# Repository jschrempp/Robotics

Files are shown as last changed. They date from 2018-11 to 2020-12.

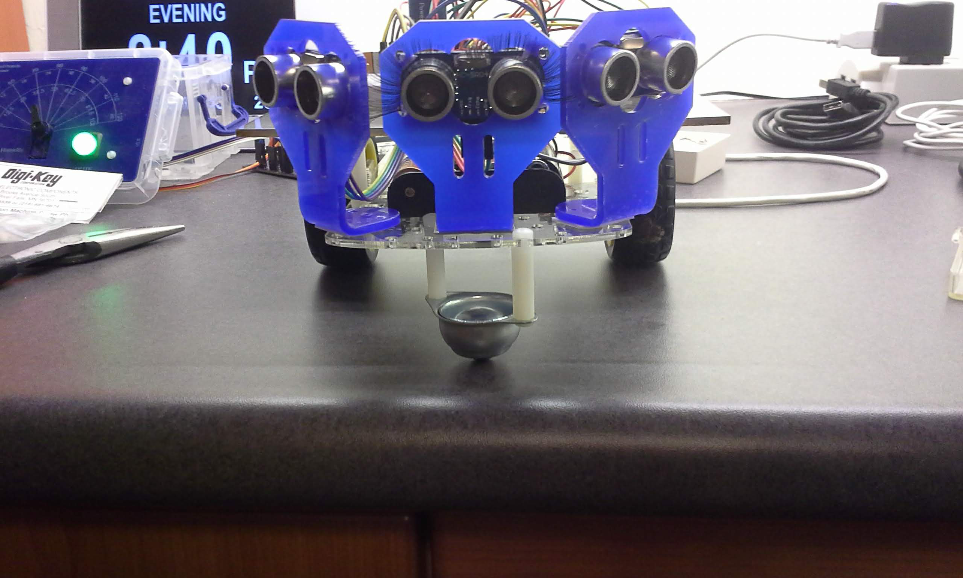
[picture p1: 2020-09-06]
Hardware/Caster_mounted_with_standoffs.jpg

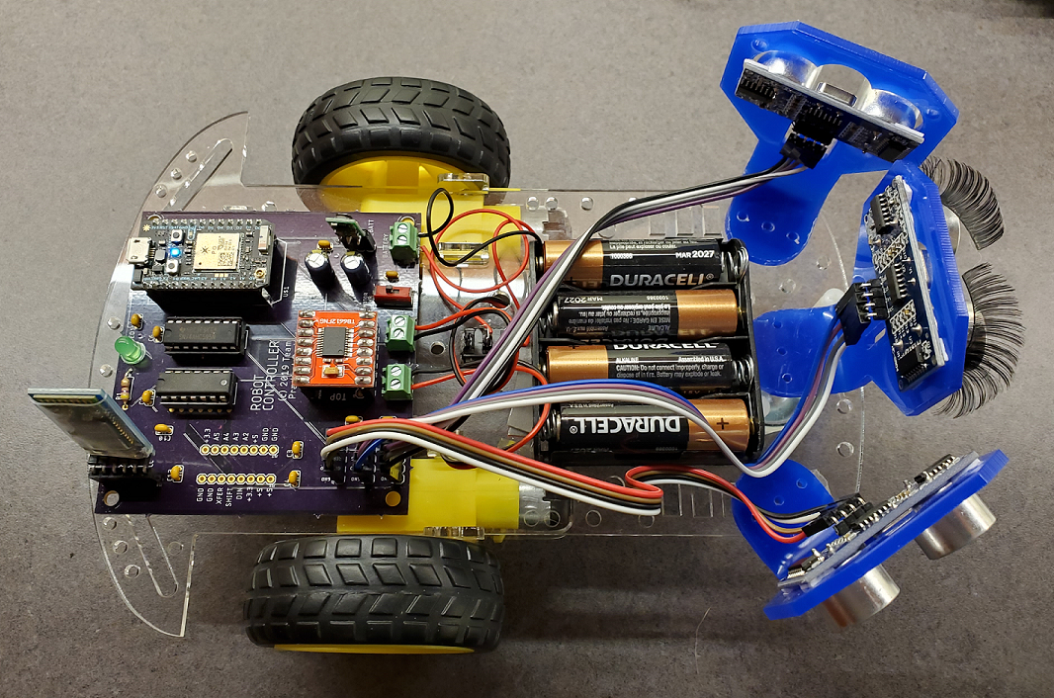
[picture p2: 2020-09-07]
Robot.png

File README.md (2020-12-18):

# Robotics
Hardware, firmware, software and documentation for low cost robotics experimentation and development using 
Particle Photon and MIT App Inventor 2.

## Story
We (Team Practical Projects) wanted to explore the capabilities and limitations of very inexpensive robot 
technology.  We obtained a basic robot kit for about $12.  This kit contains a plastic chassis, two drive
motors and drive wheels, a front caster wheel, a 4 AA cell battery holder, an on/off switch, and mounting
and assembly hardware.  

In order to run, test and explore the robot, we designed and built a Particle Photon-based printed circuit
board.  We chose the Particle Photon for our microcontroller because of Arduino
code compatibility, the ability to flash new firmware over WiFi, and Particle's IoT cloud functionality.
However, we used an inexpensive bluetooth module for basic communication with the robot (vs. the Particle Cloud)
because we wanted to experiment with our robot both indoors and outdoors; the latter where there is no
WiFi available.

The printed circuit board that we designed for this project contains all of the electronics needed to control
and monitor the robot.  This board includes:
1. The Particle Photon.
2. A buck power converter (so that the electronics can be powered from the robot's batteries).
3. Interface circuitry for three HC-SR04 ultrasonic distance sensors.
4. An HC-05 bluetooth module.
5. A dual H-bridge motor controller capable of driving the two motors on the robot.
6. Expansion capability for future development.

We wrote an Android app (in MIT App Inventor 2) to communicate with the robot and control its motion
manually and in an automatic, self-navigating, obstacle-avoiding mode.  

This repository contains complete, open source documention for building and operating this robot.

## Findings
1. The cheap caster wheel that came with the robot kit had a tendency to bind up and send the robot off
at odd angles.  Our solution was to find a suitable ball caster that replaces the robot kit front wheel.

2. In order for the robot to self-navigate, it needs to take distance measurements to obstacles both in
front of the robot and on both sides of the robot.  We tried using a single ultrasonic sensor mounted on a servo but
we found that the overall measurment cycle was too slow for our purposes.  We opted for using three, fixed
mounted ultrasonic distance sensors: one in front and two facing to each side of the robot.  These sensors
are cheap enough for us to use them this way. The side sensors are needed in the event that the robot approaches 
a side wall at a heavily oblique angle.  In particular, we have found that these sensors should face the 
side somewhere between 60 degrees and 90 degrees from the robot's front. We were unable to determine a single 
optimal angle for the side avoidance sensors.  We believe that there is too much dependancy on wall reflectivity 
and corner angles to establish a single, best sensor configuration (owning, we believe, to multi-path effects -- see below).

3. We found that there are dead spots between the three ultrasonic sensors. If the robot approaches an obstacle in 
the dead spot (e.g. a table leg), it will get hung up. We also found that the ultrasonic sensors are subject to multi-path effects.  The
ultrasonic signals can bounce off of multiple walls before returning to the sensor, resulting in incorrect distance measurements.
We also found that it is possible for a multi-path signal reflection from one sensor to be detected by another
sensor.  We created a delay of 1 millisecond between sensor readings in order to reduce this effect.  

4. We found that different surfaces reflect different amounts of ultrasonic energy.  Some surfaces (generally
soft surfaces) are poor reflectors of ultrasonic signals while other surfaces (generally hard surfaces) perform much better.
Unsurprisingly, the robot works best when tested against hard vertical walls set at right angles to each other.

5. Given the limitations of ultrasonic distance sensors, we investigated alternatives but we were unable to find
any suitable alternative sensors in the low cost range.  We tried infrared distance sensors that work by measuring
the strength of reflected infrared energy, but we found that the performance was highly sensitive to the color
of a surface.  White walls worked well, whereas black walls did not work at all (absorbed almost all of the
infrared energy).  We concluded that the best sensor technology would likely be lidar, but the cost of lidar
technology far exceeds the cost constriants of this project.

6. We found that weight distribution on the robot body impacts robot traction. The heaviest item on the 
robot platform are the batteries.  It would be best to place the battery holder directly over axis between
the two rear drive wheels. However, the parts don't fit well in this configuration.  The parts fit best
in the conguration shown on the photo "Robot.png" in this repository; however, traction is not
optimal with this configuration of parts.  Traction is improved by placing the printed circuit board
up front and the battery holder in the back.

7. The overall ability of the robot to self-navigate and avoid obstacles is fairly impressive, given the
limitations of the sensing capability.  The robot has the ability to find a way out from most obstacles,
including corners, chair and table legs, etc. Self navigation is not perfect, however.
The robot pivots on an axis between the rear drive wheels and not the center of the chassis, which results
in the pivot arc being longer than we had expected.  A 4 wheel
robot or a robot based on a tank chassis might obviate this problem.  Alternatively, adding a rear sensor and
firmware to back the robot out of a jam (in lieu of pivoting the robot to move out of a jam forward) might
improve this behavior.

8. The strength of the motors and the size of the drive and caster wheels limit the types of surfaces where the robot
can operate successfully.  A flat hard surface or a very low pile office carpet work well.  Plush carpet and 
height transitions do not work well with this robot. A tank chassis might allow the robot to operate over
small height transitions and on plush surfaces.

We have documented the robot's behavior in autonomous navigation mode (AUTO) in a series of six videos that 
you can view, beginning here:

https://www.youtube.com/watch?v=S9v4ddf_cKs&list=PLz4TQp3CqyALdgTUBRFCJkOn_9tXRT2St

In addition to autonomous mode, the Robot can be manually steered via the app supplied with this project.

## Conclusions
Our conclusion is that the robot can successfully navigate autonomously over a fairly wide range of challenging
conditions, given the limitations of the low cost hardware used.

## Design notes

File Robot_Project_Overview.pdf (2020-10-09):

# Robot Project Overview

By: Jim Schrempp and Bob Glicksman; v2, 10/8/2020

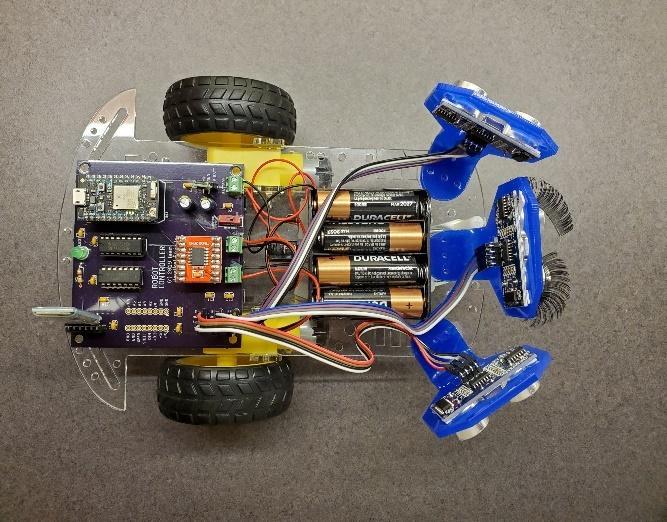
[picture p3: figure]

© 2020 Team Practical Projects, Bob Glicksman and Jim Schrempp. All rights reserved.

NOTICE: Use of this document is subject to the terms of use described in the document
“Terms_of_Use_License_and_Disclaimer ” that is included in this release package. This document can be found at:

https://github.com/TeamPracticalProjects/Robotics/blob/master/Terms_of_Use_License_and_Disclaimer.pdf

© 2020, Team Practical Projects, Jim Schrempp AND Bob Glicksman; all rights reserved. Subject to “Terms of Use, License and Disclosure”

TABLE OF CONTENTS.

TABLE OF CONTENTS. | 1
1. | DOCUMENT OVERVIEW. | 2
2. | REPOSITORY OVERVIEW. | 2
| Repository Structure. | 2
| Suggested Use of the Documents. | 4
3. | ROBOT PROJECT ARCHITECTURE AND COMPONENTS. | 5

1.DOCUMENT OVERVIEW.

This document provides an overview of the Robot project. The Team Practical Projects Robot is designed for learning and entertainment. You can control the Robot manually, via an Android App, or have it navigate autonomously, sensing and avoiding obstacles as it goes. The Robot is based upon the Particle¹ Photon; an inexpensive, but advanced, 32 bit microcontroller with built-in WiFi capability. The Photon’s WiFi capability is used in this project to allow new firmware to be flashed to the Robot “over-the-air”, without the need for wired connections. The Robot itself has been designed for Bluetooth control, so that it can operate anywhere, regardless of whether a WiFi connection is present or not.

Section 2 of this document provides a guide to this Repository. The Robot is an open source project and we provide complete documentation, including source code for the Robot firmware and controlling App software, and CAD files for the printed circuit board (PCB) that holds the Robot’s electronics. We also provide a complete build and installation instruction manual and a user manual.

Section 3 of the document provides an overview of the system architecture. The “system” is very simple, consisting of the Robot hardware, the Robot’s internal firmware for the Photon microcontroller, and an Android App that is used to control and monitor the Robot.

2.REPOSITORY OVERVIEW.

This section describes the contents of this repository. This is an open source project. The files in this repository contain source code, hardware schematics and CAD files, and documentation.

Repository Structure.

GitHub.com/TeamPracticalProjects/Robotics
| -- “README.md”: the overview read-me file that is displayed on the GitHub project page. The file format is markdown (.md)
| -- “Terms_of_Use_License_and_Disclaimer”: the terms of use that you must agree
to in order to use the contents of this repository. The file format is portable document format (.pdf)
| -- “Robot_Project_Overview.pdf”: This document. The file format is portable document format (.pdf)
| -- “Robot.png”: a photo of the Robot. The file format is .png
| -- Software (folder containing all software and firmware):
| -- AI2_App (folder containing the app software)
| -- compiled (folder)
| -- “BasicRobotControl.apk”: Android install package

1 https://www.particle.io/

for the app. Load this file onto your Android smartphone and tap on it to install the app. The file format is android application package (.apk)
| -- src (folder)
| -- “BasicRobotControl.aia”: Source code for the app.
The source code is in the MIT App Inventor 2 graphical language. Import this file into your MIT App Inventor 2 IDE in order to view and/or edit the app source code. The file format is AI2 source code format (.aia).
| -- Firmware (folder containing the firmware for the Photon)
| -- “.gitignore”. This file is used to ignore some files that should not be added to your repository. It is in plain text format.
| -- “AutonomousRobotParticle.code-workspace”. This file is automatically added by the Particle Workbench IDE and you do not need to do anything with it. If you use the Particle Workbench you can open this file to restore a development environment. It is in plain text format.
| -- “project.properties”. This file is automatically added by the Particle Workbench IDE and you do not need to do anything with it. It is in plain text format.
| -- src (folder)
| -- “AutonomousRobotParticle.ino”: Particle Photon source code for the firmware that is loaded onto the Photon. The file format is Arduino source code format (.ino), which is pure text. Copy the contents of this file into the Particle Web IDE or the Particle Workbench in order to compile the firmware and flash it onto your Photon.
| -- Documents (folder containing project documentation)
| -- “Robot_Build_And_Installation_Instructions.pdf”: Document
that details how to build, install and test the project. The file format
is portable document format (.pdf).
| -- “MFG_robot_assembly_instructions.pdf”: The robot chassis manufacturer’s instruction sheet for how to assemble the robot chassis kit. The file format is portable document format (.pdf).
| -- “Robot_User_Manual”: User manual for the Robot and its associated
App. The file format is portable document format (.pdf).
| -- Hardware (folder containing project hardware files)
| -- “Robot_Parts_List.pdf”: A parts list for the Robot with links to sources for the parts. The file format is portable document format (.pdf).
| -- “Photon_Robot_View_1.jpg”: A high resolution, top view photo of the Completed Robot. The file format is JPEG (.jpg).
| -- “Photon_Robot_View_2.jpg”: A high resolution, side view photo of the Completed Robot. The file format is JPEG (.jpg).

| -- “Caster_mounted_with_standoffs.jpg”: A photo showing how the ball caster is attached to the Robot chassis. The file format is JPEG (.jpg). | -- Photon PCB (folder)
| -- Eagle_Files (folder)
| -- “RobotController.sch”: Cadsoft Eagle schematic. File format is Eagle schematic (.sch).
| -- “RobotController.brd”: Cadsoft Eagle board layout. File format is Eagle board (.brd).
| -- “Robot_Controller_PCB_Parts_List.pdf”: A parts list for the Robot PCB. The assembled PCB is itself a part on the
Robot_Parts_List in the Documents folder. The file
format is portable document format (.pdf).
| -- “Robot_Controller_Schematic.pdf”: This is a PDF version of The Robot PCB schematic, for those who don’t have Eagle. The file format is portable document format (.pdf).

Suggested Use of the Documents.

We suggest that you read the documents (.pdf files) contained in this repository in the following order:

- Terms_of_Use_License_and_Disclaimer: read and agree to everything in this document before proceeding further this this project.
- Robot_Project_Overview: read through this document to familiarize yourself with what this project is about and ensure that you can successfully complete, install and use this project before you invest further in it.
- Robot_Build_And_Installation_Instructions: follow the steps in this document to build the electronics, build the Robot chassis and install its components, install the Photon firmware, install the App software, and perform a basic test that things are working.
- Robot_User_Manual: consult this manual to learn how about the switches on the Robot and learn to use the App.

# 3.ROBOT PROJECT ARCHITECTURE AND

COMPONENTS.

The overall architecture of the Robot system is shown is figure 3-1. The major components of the system are:

- The Robot itself.
- An Android² device (phone or tablet) running the Robot control app.
- A development computer (desktop, laptop, tablet) for compiling the Robot firmware source code and flashing the resulting firmware onto the Robot’s Photon module over the Internet.

This repository contains Particle source code for the Robot. Particle’s source code is written in Particle’s firmware language which is Arduino compatible and compiled with a C++ compiler. This source code can be compiled for the Photon using either Particle’s Web IDE or Particle’s Workbench IDE. After compilation, either of these IDE’s can be used to flash the resulting executable firmware onto the Photon using Particle’s over-the-air (OTA) flashing capability via the Particle Cloud. Instructions for doing this are contained in the document “Robot_Build_And_Installation_Instructions.pdf” which can be found in the “Documents” folder in this repository. Note that the Photon uses WiFi to communicate with the Particle cloud over the Internet, so flashing of new firmware onto the Robot can only take place where the Photon has access to WiFi and where the Photon is actually on the WiFi network. Particle makes this process extremely easy and their documentation is excellent (see: https://docs.particle.io/photon/).

After firmware is flashed to the Photon, the Robot no longer has to be in WiFi range in order to operate. The Robot is battery powered and communicates with the App using Bluetooth. The firmware places the Robot’s Photon in “Semi-Automatic mode” which means that the firmware does not need to be connected to the Particle Cloud in order to operate. However, when you want to flash new firmware the Photon will need to be connected to WiFi; do this by placing the Photon into “safe mode”. Instructions for doing this are contained in the document “Robot_Build_And_Installation_Instructions.pdf” which can be found in the “Documents” folder in this repository.

2 Sorry; an iOS version of the Robot app is not available at this time.

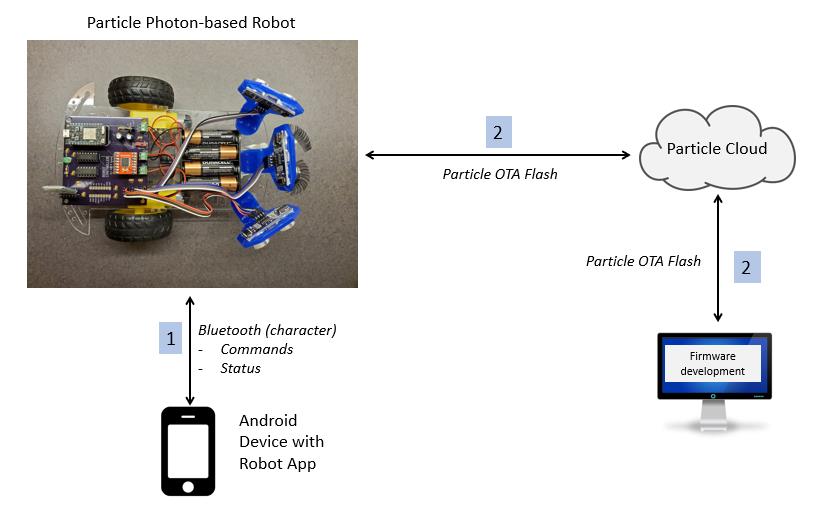
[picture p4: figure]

Figure 3-1. Robot System Components.

Figure 3-2 is a closeup photo of the Robot. The Robot consists of three major components:

- The Robot Chassis. This is a low cost kit that you purchase over the Internet. It contains the Robot body and mounting hardware, two motors with encoders and wheels, a front caster wheel (which is not used; we replace this with a ball caster for better performance), a 4 – AA battery holder, and a power on/off switch.
- The Robot PCB. This printed circuit board (PCB) needs to be assembled based upon the parts list in the Hardware/Photon PCB folder in this repository.
- Ultrasonic Distance Sensors: The Robot uses three HC-SR04 ultrasonic distance sensors for autonomous navigation. The sensors and their mounts are included in the “Robot_Parts_List.pdf” document in the Hardware folder in this repository.

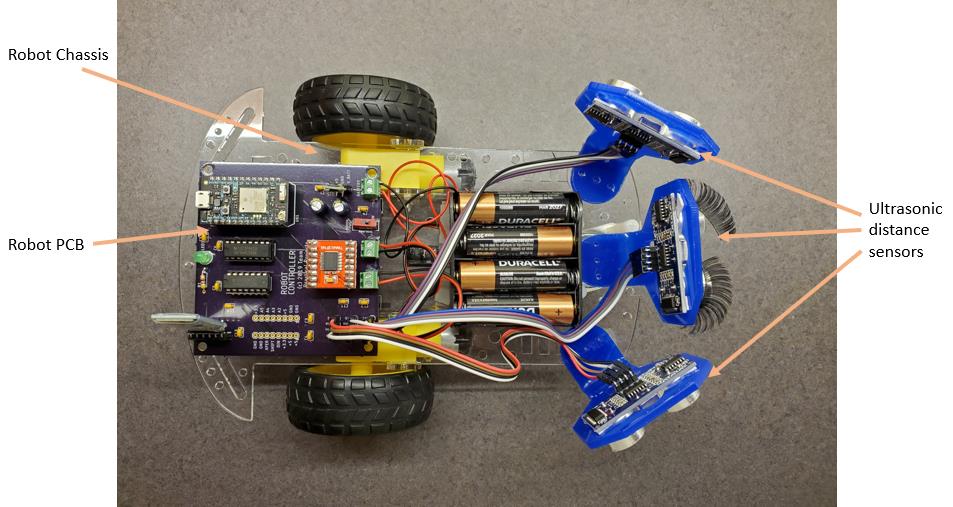
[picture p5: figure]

Figure 3-2. Robot closeup.

The final component of this Robot System is an app that runs on an Android device (phone or tablet). A screen shot of the App (in AUTO mode) is given in figure 3-3. Instructions for using the App are contained in the document “Robot_User_Maual.pdf” which is in the Documents folder in this repository.

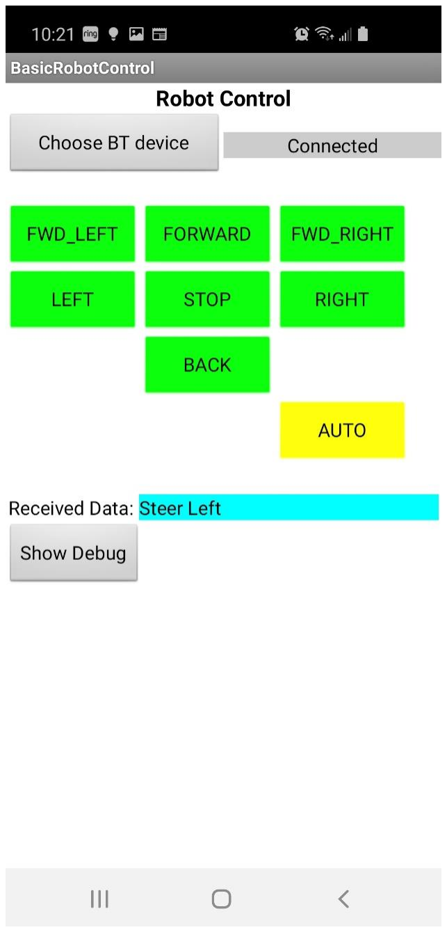
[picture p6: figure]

Figure 3-3. App screen shot (AUTO mode).

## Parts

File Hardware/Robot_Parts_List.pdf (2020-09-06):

ITEM | QTY | DESCRIPTION | VENDOR | LINK | UNIT COSTEXTENDED COST | ALTERNATE | NOTES
1 | 1 Robot Kit | ebay | https://www.ebay.com/itm/New-Smart-Motor-Robot-Car-Battery-Box-
Chassis-Kit-Speed-Encoder-For-
| | | | Arduino/233251245264?_trkparms=aid%3D555018%26algo%3DPL.SIM%26 ao%3D2%26asc%3D225074%26meid%3D354efebec4a74c81bac7d57ae2ba 87a6%26pid%3D100677%26rk%3D2%26rkt%3D30%26mehot%3Dnone%26s d%3D223697370099%26itm%3D233251245264%26pmt%3D1%26noa%3D0 %26pg%3D2386202%26algv%3DSimplAMLv5PairwiseWeb&_trksid=p23862

02.c100677.m4598 (https://www.ebay.com/itm/New-Smart-Motor-Robot-Car-Battery-Box-Chassis-Kit-Speed-Encoder-For-Arduino/233251245264)

$11.99 | $11.99

2

1

Robot Electronics PCB | Team Practical
Projects
| https://github.com/TeamPracticalprojects/Robotics/tree/master/Hardware | $104.02 | $104.02 | Build from our instructions and parts list. Most of the cost is in the bare PCB. These can be obtained for much lower price, e.g. from JCLPCB.com
3 | 1 HC_SR04 Ultrasonic Distance
Sensor
Amazon (Aokin) | https://www.amazon.com/dp/B07V6X647X/ref=dp_prsubs_3 | $7.99 | $7.99 | Get 5 pcs - need 3 pcs for robot
4 | 1 HC_SR04 Mount | Amazon (SenMod) https://www.amazon.com/gp/product/B01FDGU0GY/ref=ppx_yo_dt_b_asi
| n_title_o01_s00?ie=UTF8&psc=1 (https://www.amazon.com/gp/product/B01FDGU0GY/ref=ppx_yo_dt_b_asin_title_o01_s00?ie=UTF8&psc=1) | $7.99 | $7.99 | Get 5 pcs - need 3 pcs for robot
5 | 1 Ball Caster | Amazon
(Quickbuying)

https://www.amazon.com/gp/product/B07H5HC232/ref=ppx_yo_dt_b_asi
n_title_o00_s00?ie=UTF8&psc=1 (https://www.amazon.com/gp/product/B07H5HC232/ref=ppx_yo_dt_b_asin_title_o00_s00?ie=UTF8&psc=1)
$13.96 | $13.96 | Get 5 pcs - need 1 pcs for robot
6 | 1 #6 standoff, 1", F-F threaded Amazon | https://www.amazon.com/Lyn-Tron-Stainless-Steel-Female- Length/dp/B00PKI5NBI/ref=sr_1_4?crid=UX9AUCCKNWVI&dchild=1&keyw ords=Standoffs&pd_rd_r=a725047d-5a9c-4a79-93de- afee4ef9def9&pd_rd_w=ahVbR&pd_rd_wg=F3jHJ&pf_rd_p=91473338- a775-4a82-9600- 6767cae1f29a&pf_rd_r=ERK8K42QKTSWNMWN82M6&pid=tlRIAA7&qid=1 599417165&refinements=p_n_feature_twenty-eight_browse- bin%3A19043670011%2Cp_n_feature_fourteen_browse- bin%3A11433959011%2Cp_n_material_browse%3A17548970011&s=indust rial&sprefix=standoffs%2Cindustrial%2C274&sr=1-4
$21.58 | $21.58 | Get 10 pcs - need 2 pcs for robot
7 | 1 #6-32 screw, 1/4" | https://www.amazon.com/Stainless-Machine-Finish-Phillips- Threads/dp/B000FN3PKY/ref=sr_1_5?dchild=1&keywords=Screws&pd_rd_ r=6748bd84-aae1-44ee-80ad- aafba47a2747&pd_rd_w=9Gcuj&pd_rd_wg=neCmw&pf_rd_p=91473338- a775-4a82-9600- 6767cae1f29a&pf_rd_r=VT29VAKN079G8PEDE4XA&pid=H63dCos&qid=159 9417001&refinements=p_n_feature_twenty-eight_browse- bin%3A19043642011%2Cp_n_feature_fourteen_browse- bin%3A11433959011&s=industrial&sr=1-5 (https://www.amazon.com/Stainless-Machine-Finish-Phillips-Threads/dp/B000FN3PKY?pid=H63dCos&s=industrial)
$8.83 | $8.83 | Get 100 pcs - need 4 pcs for robot
8 | 1 strip of 40 female-female 6"
Adafruit | https://www.adafruit.com/products/266 | $3.95 | $3.95
9 | 4 AAA battery | Amazon | https://www.amazon.com/Duracell-CopperTop-Batteries-all-purpose-
household/dp/B00A4BBCIE/ref=sr_1_20?crid=2TTNFSC11DEIH&dchild=1&k eywords=aaa+battery&qid=1599416125&s=electronics&sprefix=AAA+batte ry%2Celectronics%2C236&sr=1-20 (https://www.amazon.com/Duracell-CopperTop-Batteries-all-purpose-household/dp/B00A4BBCIE?s=electronics)
$4.34 | $17.36
10 misc | #26 wire (red and black) | Misc
11 misc | double sided tape | Misc

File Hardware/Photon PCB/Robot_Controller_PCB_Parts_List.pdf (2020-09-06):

ITEM | QTY | DESCRIPTION | VENDOR | LINK | UNIT COSTEXTENDED COST | ALTERNATE | NOTES
1 | 1 Robot Controller PCB | OSHPark | https://oshpark.com/orders/nxFe79wD | $53.35 | $53.35 | Must purchase 3 boards for $53.35
2 | 1 Particle Photon with headers Particle | https://www.amazon.com/Particle-
| | | | Reprogrammable-Development-
Prototyping-
| | | | Electronics/dp/B016YNU1A0?ref_=b l_dp_s_web_14204923011 (https://www.amazon.com/Particle-Reprogrammable-Development-Prototyping-Electronics/dp/B016YNU1A0)
$19.00 | $19.00
3 | 2 Female header, 12 position | Pololu | https://www.pololu.com/product/1
| | | 030 (https://www.pololu.com/product/1030)
$0.79 | $1.58 https://www.digikey.com/product-
detail/en/sullins-connectorsolutions/PPPC121LFBN-RC/S7045-ND/810184 (https://www.digikey.com/product-detail/en/sullins-connector-solutions/PPPC121LFBN-RC/S7045-ND/810184)
4 | 1 74HC595 shift register, 16 pin DIP | Sparkfun | https://www.sparkfun.com/product s/13699 (https://www.sparkfun.com/products/13699)
$0.95 | $0.95 https://www.digikey.com/products/en
/integrated-circuits-ics/logic-shiftregisters/712?k=74ahc595&k=&pkeyw ord=74ahc595&sv=0&pv7=6&s=435&p v16=6512&sf=1&quantity=&ColumnSo rt=0&page=1&pageSize=25 (https://www.digikey.com/products/en/integrated-circuits-ics/logic-shift-registers/712?k=74ahc595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)
5 | 1 IC DIP socket, 16 pin | Sparkfun | https://www.sparkfun.com/product s/7938 (https://www.sparkfun.com/products/7938)
$0.50 | $0.50 https://www.digikey.com/product-
detail/en/on-shore-technologyinc/ED16DT/ED3046-5-ND/4147596 (https://www.digikey.com/product-detail/en/on-shore-technology-inc/ED16DT/ED3046-5-ND/4147596)
6 | 1 74AHCT125 level converter, 14 pin DIP | Digikey | https://www.digikey.com/products/ en/integrated-circuits-ics/logic- buffers-drivers-receivers- transceivers/704?k=74ahct125&k=& pkeyword=74ahct125&sv=0&pv7=6 &s=465&pv16=6510&sf=1&quantity =&ColumnSort=0&page=1&pageSize =25 (https://www.digikey.com/products/en/integrated-circuits-ics/logic-buffers-drivers-receivers-transceivers/704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)
$0.40 | $0.40
7 | 1 IC DIP socket, 14 pin | Sparkfun | https://www.sparkfun.com/product s/7939 (https://www.sparkfun.com/products/7939)
$0.50 | $0.50 https://www.digikey.com/product-
detail/en/on-shore-technologyinc/ED14DT/ED3045-5-ND/4147595 (https://www.digikey.com/product-detail/en/on-shore-technology-inc/ED14DT/ED3045-5-ND/4147595)
8 | 1 TB6612FNG dual motor driver module | Pololu | https://www.pololu.com/product/7
| | | 13 (https://www.pololu.com/product/713)
$3.33 | $3.33 https://www.sparkfun.com/products/1
4450 (https://www.sparkfun.com/products/14450)
9 | 2 Female header, 8 position | Pololu | https://www.pololu.com/product/1
| | | 018 (https://www.pololu.com/product/1018)
$0.59 | $1.18 https://www.digikey.com/product-
detail/en/sullins-connectorsolutions/PPPC081LFBN-RC/S7041-ND/810180 (https://www.digikey.com/product-detail/en/sullins-connector-solutions/PPPC081LFBN-RC/S7041-ND/810180)
10 | 1 5 volt step-up/step-down voltage regulator; S9V11F5 | Pololu | https://www.pololu.com/product/2
| | | 836 (https://www.pololu.com/product/2836)
$5.95 | $5.95
11 | 1 Female header, 3 position | Pololu | https://www.pololu.com/product/1
| | | 013 (https://www.pololu.com/product/1013)
$0.34 | $0.34 https://www.digikey.com/product-
detail/en/sullins-connectorsolutions/PPPC031LFBN-RC/S7036-ND/810175 (https://www.digikey.com/product-detail/en/sullins-connector-solutions/PPPC031LFBN-RC/S7036-ND/810175)

Must purchase mimimum of 5 connectors from Pololu

12 | 1 Bluetooth Module, HC-05 | Amazon (HiLetGo) https://www.amazon.com/gp/produ ct/B071YJG8DR/ref=ppx_yo_dt_b_a sin_title_o02_s00?ie=UTF8&psc=1 (https://www.amazon.com/gp/product/B071YJG8DR/ref=ppx_yo_dt_b_asin_title_o02_s00?ie=UTF8&psc=1)
$8.95 | $8.95
13 | 1 Female header, 6 position | Pololu | https://www.pololu.com/product/1
| | | 016 (https://www.pololu.com/product/1016)
$0.49 | $0.49 https://www.digikey.com/product-
detail/en/sullins-connectorsolutions/PPPC061LFBN-RC/S7039-ND/810178 (https://www.digikey.com/product-detail/en/sullins-connector-solutions/PPPC061LFBN-RC/S7039-ND/810178)

Must purchase minimum of 2 connectors from Pololu

14 | 1 Male breakable header; 0.1"
pitch; 40 position
Sparkfun | https://www.sparkfun.com/product
s/116 (https://www.sparkfun.com/products/116)

$0.00 https://www.digikey.com/product-detail/en/wurth-electronicsinc/61304011121/732-5334-
ND/4846884 (https://www.digikey.com/product-detail/en/wurth-electronics-inc/61304011121/732-5334-ND/4846884)

For connecting ultrasonic distance sensor, HC-SR04; need 12 pins total

15 | 1 LED, 5 MM | Sparkfun | https://www.sparkfun.com/product s/9592 (https://www.sparkfun.com/products/9592)
$0.35 | $0.35 | Green LED is preferred but any color will do
16 | 1 Resistor, 470 ohm (footprint: 0207/10) | Digikey | https://www.digikey.com/product- detail/en/stackpole-electronics- inc/CF14JT470R/CF14JT470RCT- ND/1830342 (https://www.digikey.com/product-detail/en/stackpole-electronics-inc/CF14JT470R/CF14JT470RCT-ND/1830342)
$0.10 | $0.10
17 | 2 Capacitor, 100 uF; footprint
E2, 5-6E
Sparkfun | https://www.sparkfun.com/product
s/96 (https://www.sparkfun.com/products/96)
$0.35 | $0.70 https://www.digikey.com/products/en
?keywords=P10269-ND (https://www.digikey.com/products/en?keywords=P10269-ND)

Electrolytic, min 20 volt rating, 0.1" center-center lead pitch

18 | 11 Capacitor, 0.1 uF; footprint
C025-024X044
Sparkfun | https://www.sparkfun.com/product
s/8375 (https://www.sparkfun.com/products/8375)
$0.25 | $2.75 https://www.digikey.com/product-
detail/en/kemet/C315C104M5U5TA/3 99-4151-ND/817927 (https://www.digikey.com/product-detail/en/kemet/C315C104M5U5TA/399-4151-ND/817927)

Ceramic, min 10 volt rating, 0.1" center-center lead pitch

19 | 3 PCB screw terminal, 2
position, 3.5 mm pitch
Sparkfun | https://www.sparkfun.com/product
s/8084 (https://www.sparkfun.com/products/8084)
$0.95 | $2.85 https://www.pololu.com/product/244
4 (https://www.pololu.com/product/2444)

https://www.digikey.com/product-detail/en/wurth-electronicsinc/691214110002/732-2747-ND/2508516 (https://www.digikey.com/product-detail/en/wurth-electronics-inc/691214110002/732-2747-ND/2508516)
20 | 1 PCB mount switch, SPDT
(11.6x4.0 mm)
Sparkfun | https://www.sparkfun.com/product
s/9609 (https://www.sparkfun.com/products/9609)
$0.75 | $0.75 https://www.pololu.com/product/140
8 (https://www.pololu.com/product/1408)

https://www.digikey.com/product-detail/en/nkkswitches/SS12SDP4/360-2922-ND/1054800 (https://www.digikey.com/product-detail/en/nkk-switches/SS12SDP4/360-2922-ND/1054800)

TOTAL | $104.02

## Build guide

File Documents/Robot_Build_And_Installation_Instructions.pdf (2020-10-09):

# Robot Build and Installation Instructions

By: Jim Schrempp and Bob Glicksman; v3, 10/8/2020


© 2020 Team Practical Projects, Bob Glicksman and Jim Schrempp. All rights reserved.

NOTICE: Use of this document is subject to the terms of use described in the document
“Terms_of_Use_License_and_Disclaimer ” that is included in this release package. This document can be found at:

https://github.com/TeamPracticalProjects/Robotics/blob/master/Terms_of_Use_License_and_Disclaimer.pdf

© 2020, Team Practical Projects, Jim Schrempp AND Bob Glicksman; all rights reserved. Subject to “Terms of Use, License and Disclosure”

TABLE OF CONTENTS.

TABLE OF CONTENTS. | 1
1. | OVERVIEW. | 2
2. | ROBOT PCB ASSEMBLY INSTRUCTIONS. | 4
3. | ROBOT ASSEMBLY INSTRUCTIONS. | 14
3.1. | Robot Chassis. | 14
3.2. | Robot Wiring. | 17
3.3. | Power Up Testing. | 21
4. | FIRMWARE INSTALLATION INSTRUCTIONS. | 22
5. | ROBOT APP INSTALLATION INSTRUCTIONS. | 24

1.OVERVIEW.

This document provides step-by-step instructions for assembling and installing the Robot hardware, firmware and app software. Before proceeding with this project, you must read and accept the “Terms_of_Use_License_and_Disclaimer” document which is located in the root level of this repository.

The parts needed to build this project are illustrated in figure 1-1 and are described below:


Figure 1-1. Complete Robot Assembly.

- Robot PCB: assembled printed circuit board with electronics to control the Robot. Section 2 of this document contains the details.
- Robot Chassis: this is a kit that must be assembled according to the instructions in section 3 of this document.
- Ultrasonic Sensors (SR-HC04). The Robot navigates based upon data from three ultrasonic distance sensors. These sensors are mounted on the Robot chassis using commercially available mounting brackets; see section 3 of this document for details.
- Batteries: The Robot is powered by 4 – AA batteries. The Robot kit contains the necessary battery holder.

The following tools and materials are needed to build this project. Make sure that you know how to use these before undertaking this project!

- Small tip soldering iron.
- Electrical solder.
- A few feet of #26 solid, insulated wire. It will be helpful to use two different colors, e.g. red and black.
- Female-female jumper cables, 9” long.
- Wire stripper.
- Diagonal wire cutter.
- Needle nose pliers.
- Various screwdrivers.
- Electrical tape.
- Hot glue gun with glue sticks or double sided tape (for mounting)

Our recommended order of assembly is as follows.
A. Assemble the Robot PCB with the necessary components for this project – see section 2 of this document.
B. Assemble and wire the Robot chassis from the kit – see section 3 of this document.
C. Mount the ultrasonic distance sensors and Robot PCB on the Robot chassis - see section 3 of this document.
D. Wire up the power, sensors, and Robot motors to the Robot PCB – see section 3 of this document.
E. Install Photon firmware – see section 4 of this document.
F. Install the App on your smartphone – see section 5 of this document.

2.ROBOT PCB ASSEMBLY INSTRUCTIONS.

The Robot PCB contains all of the electronics needed to control the Robot, except for the power on/off switch, the ultrasonic distance sensors, and the batteries. This section contains step-by-step instructions for assembling the Robot PCB.

Figure 2-1 shows the blank PCB. This is the top side of the board – the side where all of the components are mounted. All soldering is performed on the bottom side of the PCB.

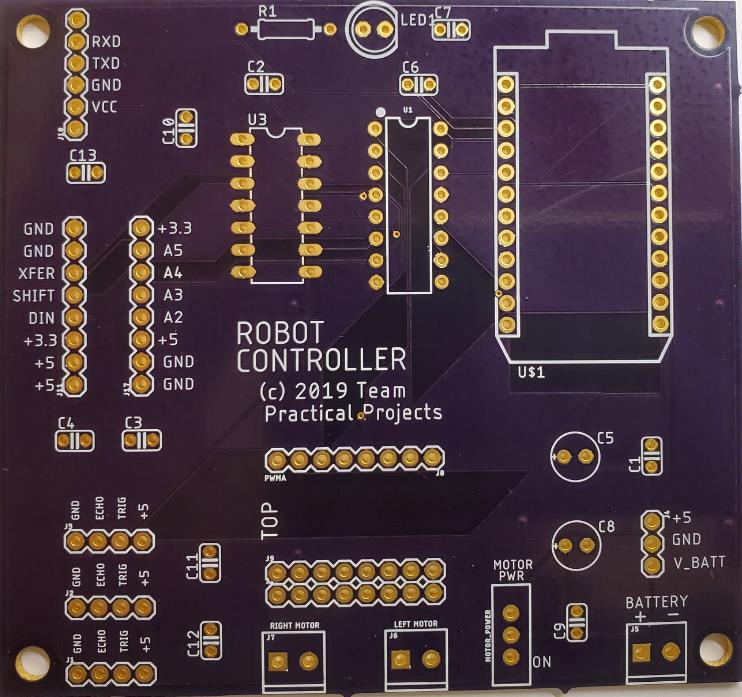
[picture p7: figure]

Figure 2-1. Blank Robot PCB.

We recommend that the board be assembled according to the height of the component, shortest components first. This is because it may be necessary to hold some of the components on the PCB with electrical tape while soldering and we don’t want tall components to get in the way.

The first step is to place 11 ea. 0.1 uF decoupling capacitors onto the component side of the PCB with the leads sticking through the holes in the board – see figure 2-2. Bend the leads over on the bottom of the PCB to hold these capacitors in place. Solder the capacitor leads to the PCB and clip the excess leads off with a diagonal cutter.

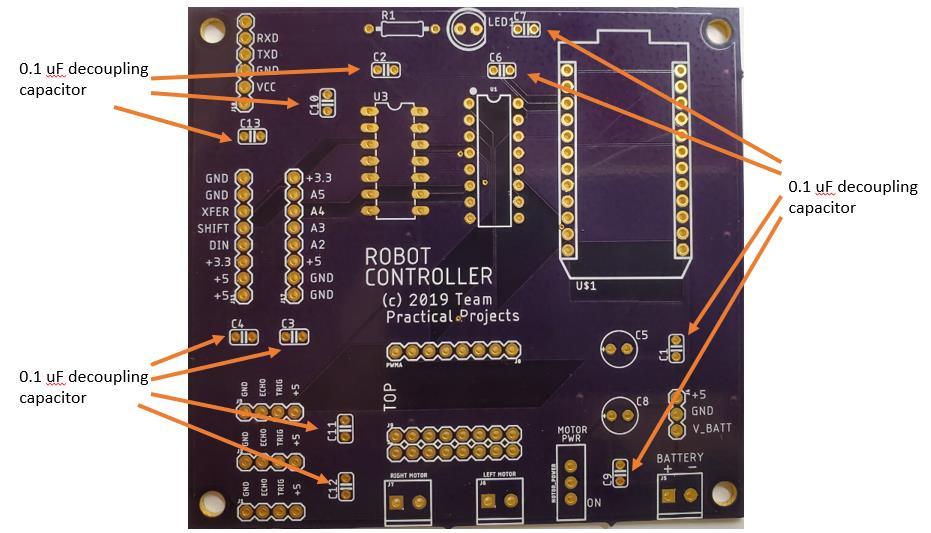
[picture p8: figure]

Figure 2-2. Decoupling Capacitors.

The next set of components to be soldered onto the PCB are shown in figure 2-3. Place the 14 pin DIP socket on the PCB where shown (U3). Make sure that the little notch on the socket aligns with the notch shown on the PCB silkscreen. Hold the socket fast to the PCB with electrical tape. Invert the board and solder two diagonally opposite pins first to hold the socket in place. Then solder the remaining pins to the PCB. Next, repeat this process for the 16 pin DIP socket (U1).

Place three, 2-position terminal blocks on the PCB with the wire holes facing the outside of the PCB. Hold each of these terminal blocks, in turn, to the PCB using some electrical tape. Note that the terminal blocks can wiggle a little in the PCB holes. Try and align each terminal block to face straight outward before inverting the PCB and soldering the pins to the bottom of the PCB.

Place the PCB slide switch on the PCB in the area indicated as “MOTOR PWR”. Hold it fast to the PCB with electrical tape; invert the PCB and solder the leads to the bottom of the board.

Place the 470 ohm resistor on the PCB in the place marked R1. Bend the leads over on the bottom of the PCB to hold the resistor in place. Solder the leads and clip off the excess with a diagonal cutter.

Lastly, place the LED where indicated on the PCB. CAREFULLY note the flat part of the outline on the top of the PCB. Make sure that the flat part of the LED aligns with the marking on the PCB. Bend the LED leads over to hold it in place and double check the LED placement. Then solder the leads to the bottom side of the PCB and clip off the excess with a diagonal cutter.

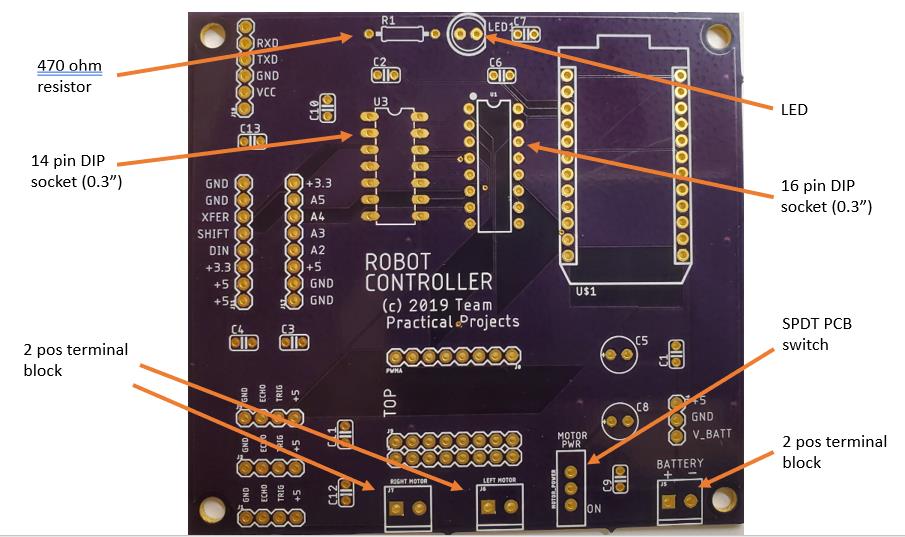
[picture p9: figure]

Figure 2-3. LED/Resistor, DIP sockets, Switch, Terminal Blocks.

The next step is to solder the female headers to the PCB; refer to figure 2-4. Begin with the 6 pin female header for the Bluetooth module shown in the upper left of figure 2-4. Place the header through the PCB and hold it in place with some electrical tape. Try and tape the header down so that it is vertical on the PCB. After aligning and taping the header to the PCB, invert the board and solder the two end pins to hold it in place. The solder the remaining pins.

Next, solder in the 3 pin female header for the voltage regulator. This is the header shown at the bottom right side of figure 2-4. Place the header through the PCB and hold it in place with some electrical tape. Try and tape the header down so that it is vertical on the PCB. After aligning and taping the header to the PCB, invert the board and solder the three pins to the PCB.

The next step is to solder the headers for the motor controller to the PCB. Two sets of 8-pin female headers are used. Note that three sets of headers are provided for on the PCB. The PCB supports two different modules that use the TB6612FNG dual motor controller chip. The modules differ only in the module width – one is 0.5” wide and the other is 0.6” wide. You do not need to worry about this as the headers will be soldered with your motor controller module in place. However, do make note that there will be an extra row of headers that are not soldered when your motor controller assembly is complete. This is normal and of no concern.

Solder male pins to the motor controller board so that the main components of the motor control board are facing upward (away from the pins); refer for figure 2-9 for example. Now place two 8-pin female headers into the pins on the bottom of your motor control module. The module orientation does not matter at this point as this assembly step is only needed to align the female pin headers when soldering them to the PCB. Now place the motor controller female headers down through the PCB and use some electrical tape to hold the motor controller and its female headers fast to the PCB. Invert the PCB and solder the 4 end pins (two on each female header) to hold the headers in place. Carefully, unplug the motor controller module from the female headers and set it aside. Now, solder the rest of the female header pins to the PCB.

The next step is to solder the headers for the Particle Photon to the PCB. Two sets of 12-pin female headers are used. Place the two 12-pin female headers into the pins on the bottom of The Photon. The Photon orientation does not matter at this point as this assembly step is only needed to align the female pin headers when soldering them to the PCB. Now place the Photon female headers down through the PCB and use some electrical tape to hold the Photon and its female headers fast to the PCB. Invert the PCB and solder the 4 end pins (two on each female header) to hold the headers in place. Carefully, unplug the Photon from the female headers and set it aside. Now, solder the rest of the female header pins to the PCB.

Lastly, place two 100uF filter capacitors through the holes for C5 and C8 on the PCB, as indicated in figure 2-4. Note that these capacitors are polarized and must be inserted in the correct orientation. The capacitors have a silver stripe down one side – this is the minus (-) terminal of the capacitor. The PCB indicates the positive (+) lead with a little “+” sign. The capacitor lead that is NOT where the silver strip is goes in the hole marked “+”. The lead by the silver stripe goes through the unmarked hole on the PCB. In other words, the silver stripe on the C5 capacitor should be facing the C1 decoupling capacitor, and the silver stripe on the C8 capacitor should be facing the 3 pin female socket for the voltage regulator. Bend the leads over on the bottom of the PCB to hold the capacitors in place and double check the mounting polarity. Now, solder the leads to the bottom side of the PCB and clip off the excess leads with a diagonal cutter.

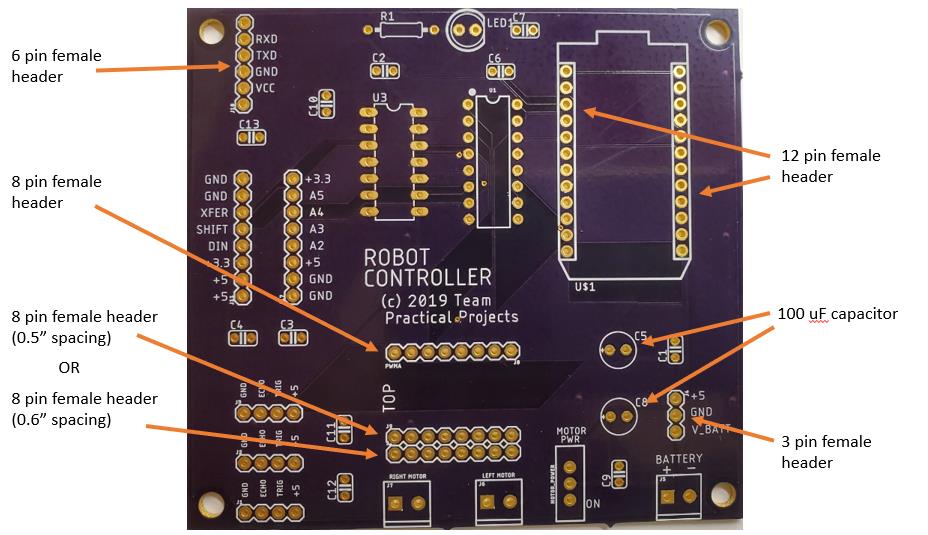
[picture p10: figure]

Figure 2-4. Filter Capacitors, Female headers.

The last soldering step involves soldering male pin headers to the PCB; see figure 2-5. The male pin headers come in a long strip and you use a pair of needle nose pliers to break off the number of pins that you need for each pin header connector. You will need three, 4-pin headers for this step. Note that the PCB has two additional fields for 8-pin male pin headers. These are provided for possible future expansion of the electronics and you do not have to solder these optional pin headers onto the PCB at this time. We recommend that you solder in only the three, 4-pin headers.

We suggest that you insert and solder one of these 4-pin headers to the PCB at a time. Break off the pin header and place it through the holes on the PCB. Use electrical tape to hold the pin header to the PCB for soldering. NOTE: try and tape the headers to the PCB so that they are vertical. This is tricky to do but it will make the board a lot neater if you are careful with this step!

After taping a 4-pin male header to the PCB, invert the board and solder the two end pins first. Then solder the two middle pins. Repeat this process for the remaining two 4-pin headers.

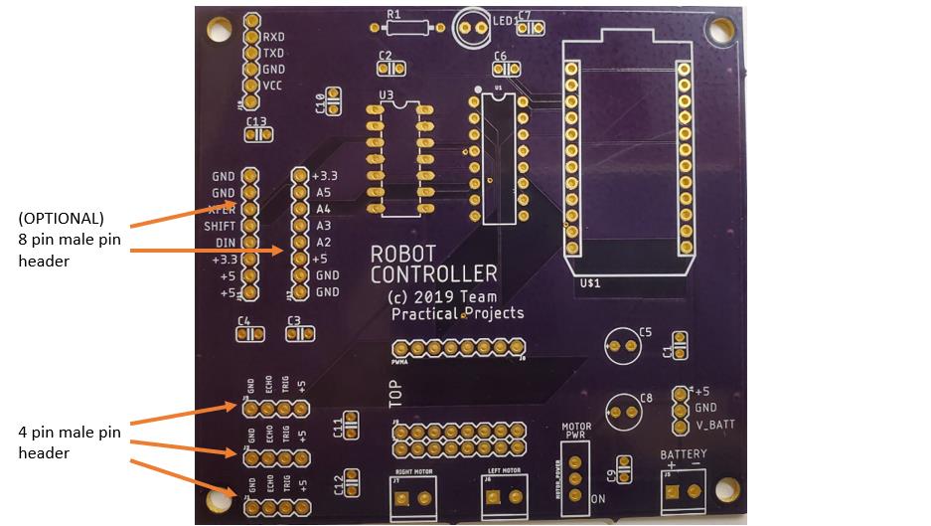
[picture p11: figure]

Figure 2-5. Male Pin Headers.

Congratulations! You have completed soldering components to the PCB. Carefully inspect all solder joins to ensure that there are no cold solder joints and no solder shorts on the bottom of the board. Clean off excess solder from the bottom of the board and inspect carefully one more time.

All that remains is to insert the socket components into their sockets on the PCB. Insert the Photon onto the PCB with the USB connector facing off of the board – see figure 2-6.

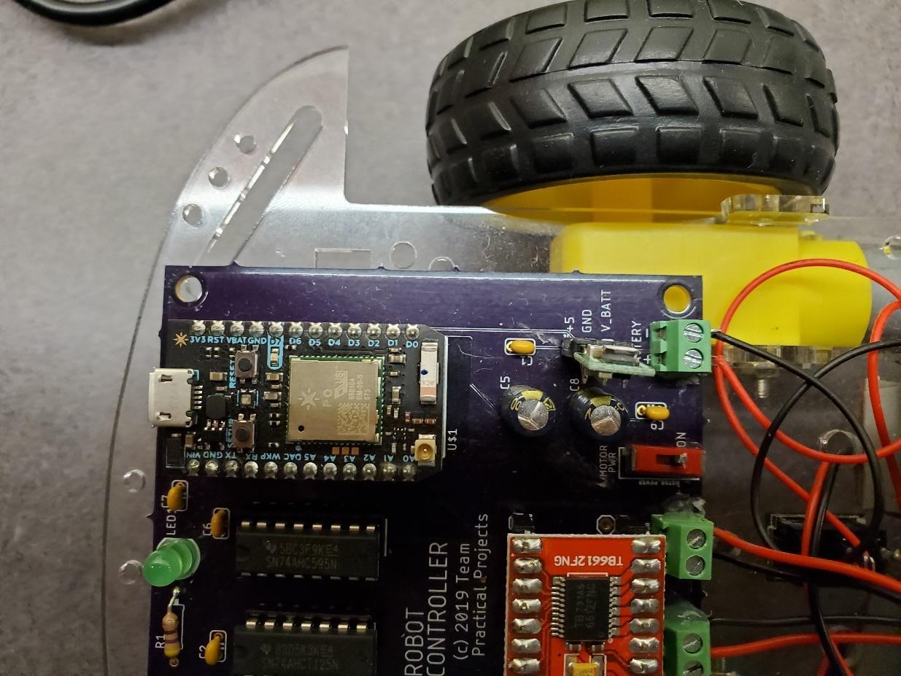
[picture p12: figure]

Figure 2.6. Positioning the Photon.

Next, plug the HC-05 bluetooth module into its 6-pin socket with the component side facing out from the board; i.e. the writing side facing onto the board – see figure 2-7.

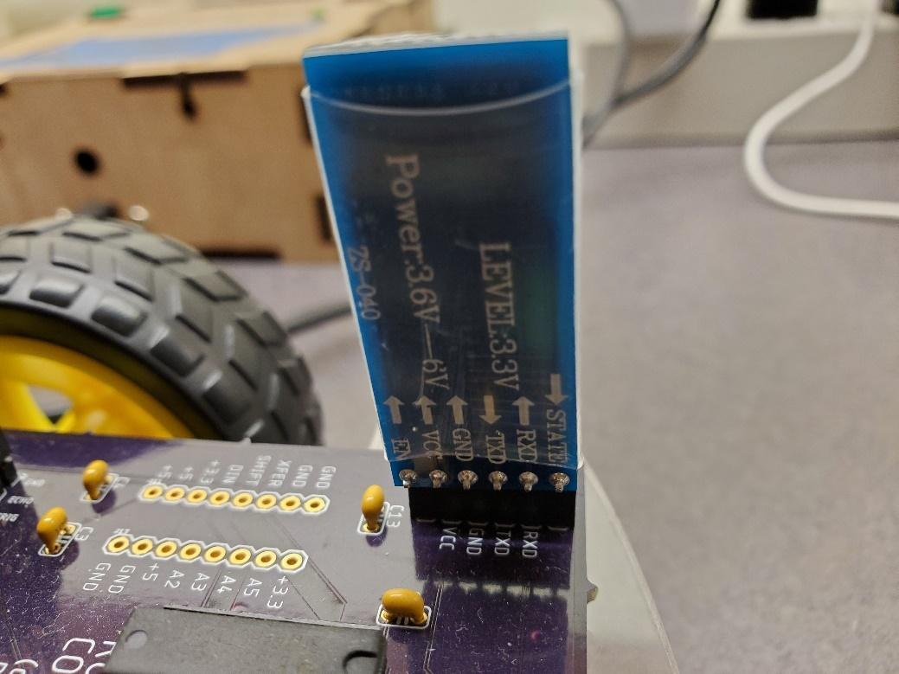
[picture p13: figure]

Figure 2-7. Positioning the Bluetooth Module.

You may need to solder pins into the Pololu voltage regulator module. Solder the right angle pin header onto the module so that the connector is on the side of the module as shown in figure 2-8 and solder the connector pins to the reverse side of the module. After soldering pins to the voltage regulator module, plug it into the 3 pin female header on the PCB as shown in figure 2-
8. Double check that this module is inserted into the header in the proper orientation.

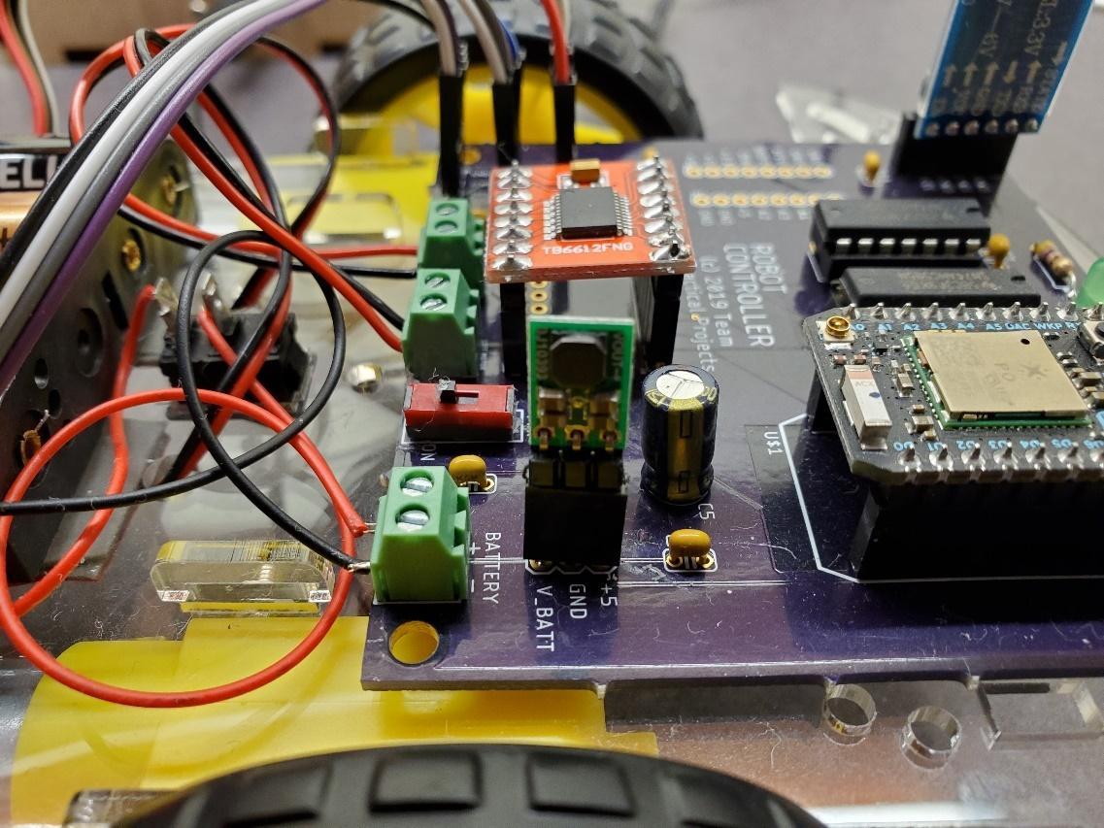
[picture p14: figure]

Figure 2-8. Positioning the Voltage Regulator.

Plug the motor controller module onto the PCB as shown in figure 2-9. Double check to ensure that the module is oriented exactly as shown in figure 2-9.

Plug the 74AHCT125 IC into the 14 pin DIP socket on the PCB. Make sure that the notch or dot on the IC faces where the notch on the socket is and ensure that all pins of the IC are properly inserted into the socket and not bent under the IC. Double check the orientation as in figure 2-
9. Lastly, plug the 74HCT595 IC into the 16 pin DIP socket on the PCB. Make sure that the notch or dot on the IC faces where the notch on the socket is and ensure that all pins of the IC are properly inserted into the socket and not bent under the IC. Double check the orientation as in figure 2-9.

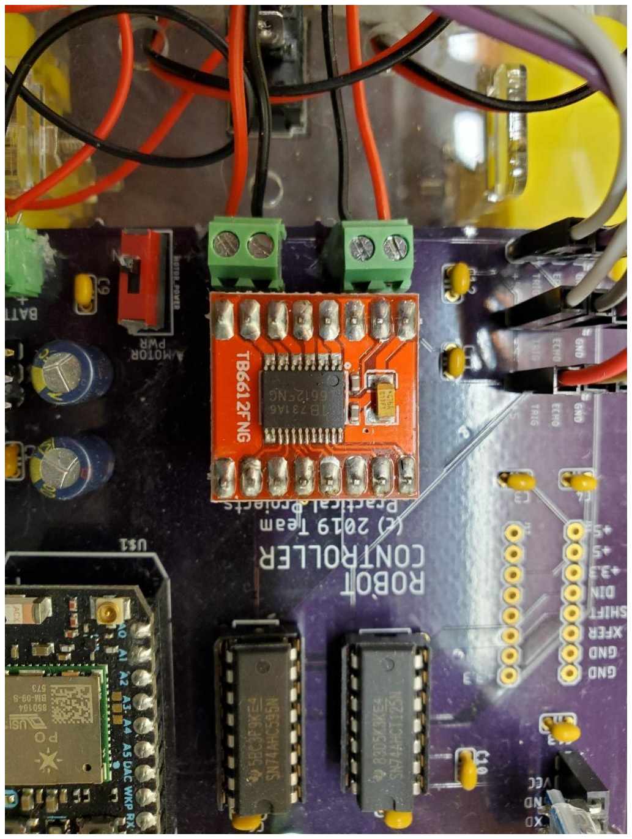
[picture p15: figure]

Figure 2-9. Positioning the Motor Controller and Socketed ICs.

The PCB assembly is now complete!

3.ROBOT ASSEMBLY INSTRUCTIONS.

This section provides detailed instructions for assembling and wiring the Robot. The first step is assembling the Robot chassis from the Robot kit that you purchased. The battery holder, ultrasonic distance sensors and the Robot PCB are added later. These components are then wired up to complete the Robot assembly.

3.1. Robot Chassis.

Your Robot chassis kit should have come with assembly instructions. We have posted a copy of the instructions that came with our Robot in the file “MFG_robot_assembly_instructions.pdf” in this folder. The text is in Chinese, but the pictures should be self-explanatory. When assembling the Robot chassis, you may skip the step of attaching the front caster wheel as you will replace this with the ball caster wheel anyway.

We strongly recommend that you solder wires to the Robot motors before attaching the motors to the chassis. We recommend that you use #26 solid copper wire for these connections. Take care, as the terminals on the motors are rather delicate. You may want to use different color wires for the terminals on the motors to help you decide which wire goes to which terminal on the PCB’s motor terminal blocks. However, you will be testing for proper motor wiring when the assembly is finished and you can always reverse the motor wires if necessary. The motor control wires are not polarized, but they do determine which way the motor spins when commanded to do so by the Photon’s firmware. If, in testing, a motor spins backward from the way it should spin, you can simply reverse the motor wires in the terminal block in the PCB to correct the problem.

Next, assemble the ball caster to the front of the Robot chassis. Figure 3-1 shows the assembly of the ball caster.

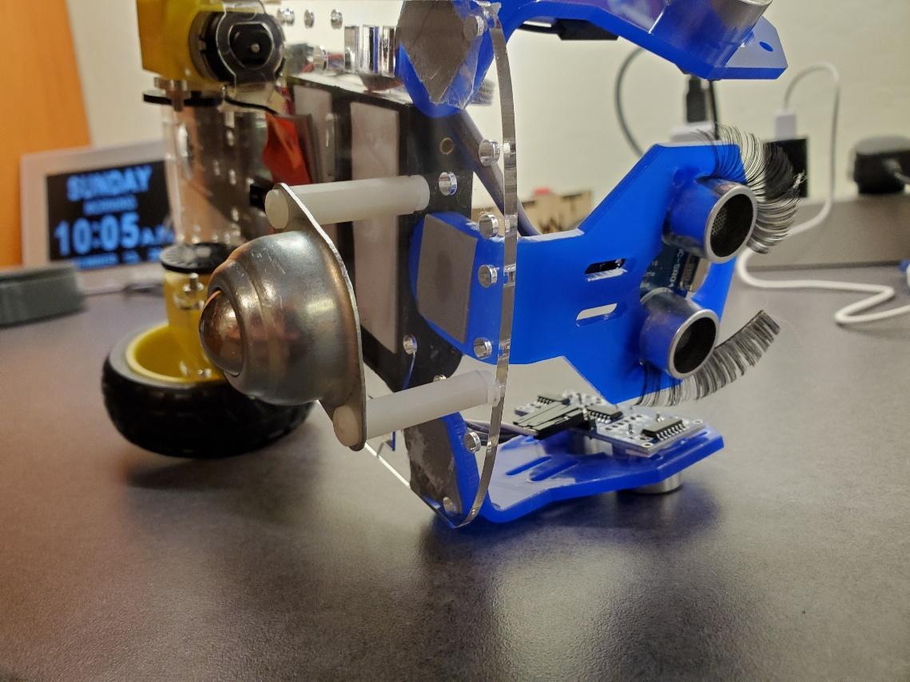
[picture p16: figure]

Figure 3-1. Front Wheel Assembly using Ball Caster.

Attach two, 1” threaded female-female standoffs on the ears of the ball caster using #6 screws. Do not tighten the screws at this point. Align the standoffs with two diagonally facing screw holes in the chassis that are intended for the kit’s caster wheel. Use two #6 screws to affix the standoffs to the chassis. Tighten all of the screws to complete the caster wheel assembly step.

Figure 3-2 shows the completed assembly of the Robot. To complete Robot assembly, you will be adding the power switch, the battery holder, the PCB and the three ultrasonic sensors to the chassis.

Figure 3-2. Completed Robot Assembly.

First, make sure that you have pressed the power switch that comes with the Robot kit into the hole provided in the chassis. You should have done this when assembling the robot chassis per the kit instructions. We suggest that you mount this switch upside down – i.e. with the switch control on the Robot’s underside and the switch terminals on the top side of the Robot chassis. This will make power wiring a little easier; however, either way that you mount the switch will work.

Next, place the battery holder on the top of the robot chassis approximately where shown in figure 3-2. Use double sided tape or hot glue to affix the battery holder to the Robot chassis. Make sure that the battery wires face the rear of the Robot (i.e. face the power switch and the PCB).

Next, place the Robot PCB (that you assembled in section 2 of this document) on the Robot chassis, approximately as shown in figure 3-2. Make sure that the terminal blocks face the front of the Robot. Use double sided tape or hot glue to affix the PCB to the Robot chassis.
Next, strip three, 4-lead cables from the 9” long female-female ribbon cable in the parts list. Take the three SR-HC04 ultrasonic distance sensors and place the four wires of each cable onto the pins on each sensor, carefully noting which color wire goes to which signal. The four signals on each ultrasonic sensor are marked on the back of the sensor, as follows:
- Gnd
- Echo
- Trig
- Vcc

You will need to know which color wire (from each sensor) is associated with each of these signals later, when wiring the sensors to the Robot PCB.

Now that you have placed a 4-wire cable on each ultrasonic sensor, place each sensor in a holder, as shown in figure 3-2. Use hot glue or double sided tape to affix the sensor to the holder. Take care that the cable runs freely from each sensor after assembling to the holder.

Place one of the ultrasonic distance sensors at the front of the robot, approximately in the center and as far forward as it will mount securely to the Robot chassis. Use hot glue or double sided tape to affix the sensor holder to the Robot chassis; see figure 3-2. Place the other two sensors to either side of the front sensor with each side sensor facing approximately 45 – 60 degrees from the front of the Robot. Use hot glue or double sided tape to affix the sensor holder to the Robot chassis; see figure 3-2.

The Robot chassis assembly is now complete. In the next step, you will wire up the power, the motors and the three ultrasonic sensors to the Robot PCB.

3.2. Robot Wiring.

Figure 3-3 is a closeup view of the top of the Robot after wiring is complete. Figure 3-4 is a bottom side view of the wired Robot. Figure 3-5 shows the wire connections to the Robot PCB. Refer frequently to these figures when wiring the Robot.

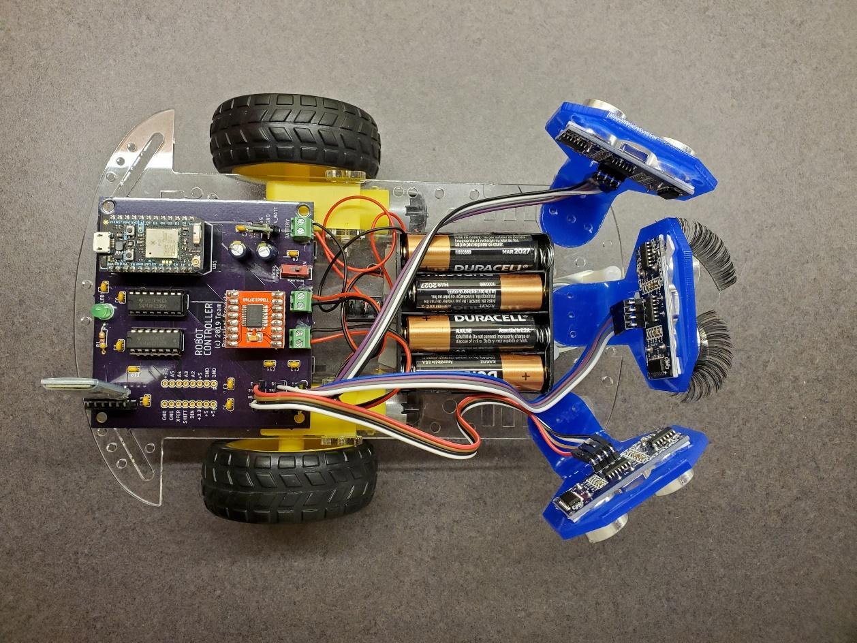
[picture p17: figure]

Figure 3-3. Top View of Wired Robot.

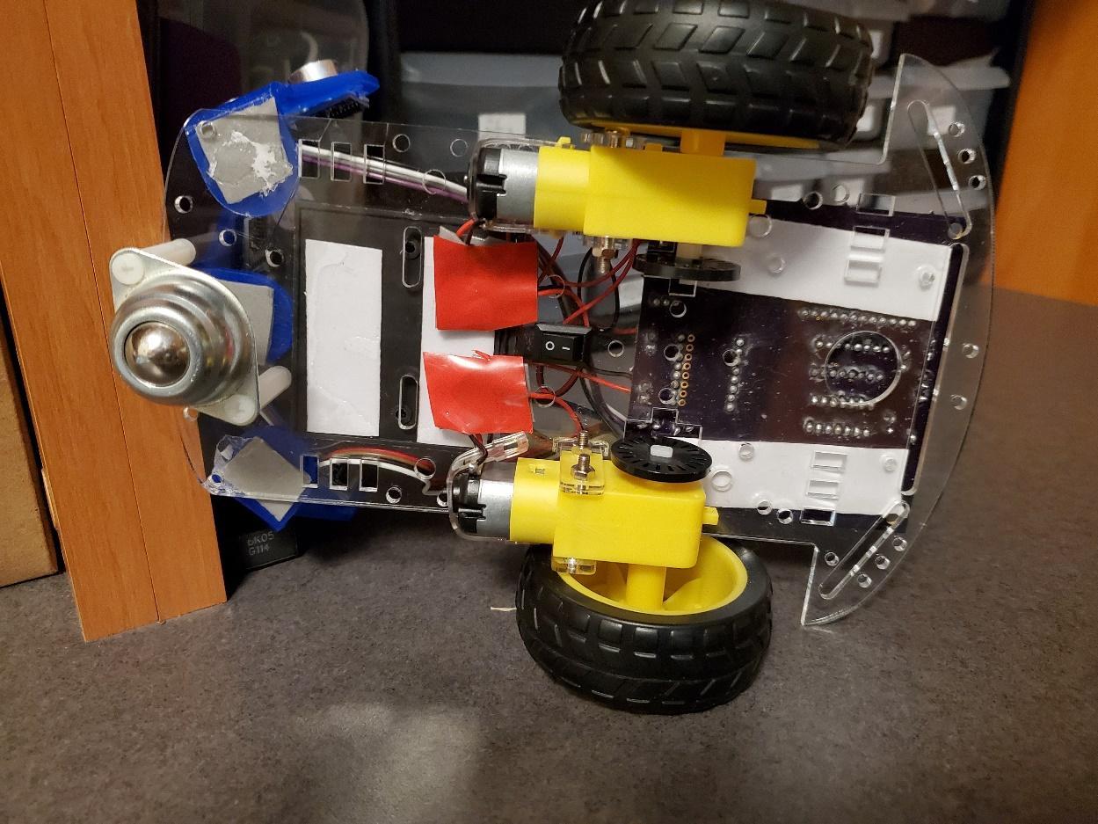
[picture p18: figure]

Figure 3-4. Bottom View of Wired Robot.

Figure 3-5 shows the wire connections to the Robot PCB.

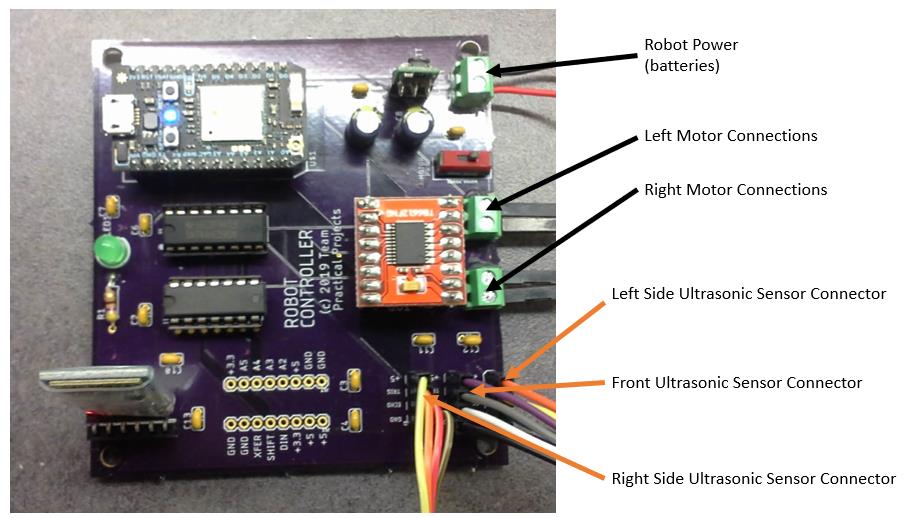
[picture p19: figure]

Figure 3-5. Wire Connections to the Robot PCB.

Step 1: Battery (Power) wiring. The battery holder has two wires: a red wire and a black wire. The black wire is connected to the “-“ terminal of the BATTERY terminal block on the PCB. The red wire from the battery holder is soldered to the power switch on the chassis (outside terminal). Solder a (red) wire to the center terminal of the power switch and connect the other end of this wire to the “+” terminal of the BATTERY terminal block on the PCB. We suggest trimming these wires back so that they are only a little longer than necessary to make these connections. Make sure that the black and red wires are properly placed into the BATTERY terminal block connections and tighten down the screws on the terminal block to secure these connections.
Step 2: Motor wiring. You should have soldered wires to the left and right motor terminals when assembling the Robot chassis. Use tape or hot glue to fasten these wires to the underside of the Robot chassis in order to provide mechanical strain relief – see figure 3-4. Thread the wires from the left motor through a hole in the chassis to the left of the power switch so that the wires are now available on the top side of the chassis. Wire these to the LEFT MOTOR terminal block. Do the same with the wires from the right side motor, except that the chassis through hole is to the right of the power switch and the wires are connected to the RIGHT MOTOR terminal block on the Robot PCB. NOTE: the motor wires are not polarized; however, they do determine the direction that the motor spins. We will test this out when the Robot assembly is completed and if one (or both) of the motors spins in the reverse direction that it should, simply reverse that motor’s wires in the terminal block. Make sure that the wires are properly placed into the terminal block connections and tighten down the screws on the terminal block to secure these connections.

Step 3: Ultrasonic Sensor wiring. You should have three, 4-wire female ribbon cables from the three ultrasonic sensors. The left side sensor is connected to the frontmost (near the terminal blocks) male pin header field. The right side sensor is connected to the rearmost (back from the terminal blocks) male pin header field. The front sensor is connected to the middle male pin header field. You should have noted the color wire from each sensor associated with the Gnd, Echo, Trig and Vcc connections on the sensor. Starting with the left side sensor, plug each female connector of the ribbon cable onto the pin corresponding to that signal on the Robot PCB. After wiring the left side sensor, wire the front sensor next and finally wire the right side sensor. Double check all connections to be sure that they are fully inserted onto the proper male pin.
3.3. Power Up Testing.

Now that your Robot is fully wired, you should test that it powers up correctly. First, make sure that the Robot power switch is turned OFF. Next, install four AA batteries in the battery holder. Double check that you have set the batteries in the right orientation. Go back and check that you have the Pololu voltage regulator, the motor driver module, the Bluetooth module, the Photon and the ICs plugged into their sockets correctly. Double check that you have the battery “+” (from the power switch) and the battery “-“ leads connected correctly in the BATTERY terminal block. After completing all of the checks, turn the Robot power switch ON. You should see:

- A flashing red light on the Bluetooth module.
- The multicolor LED on the Photon either flashing or “breathing” some color. The behavior depends upon the previous state of the Photon. What is important here is that there is some indication of power to the Photon.

If you do not see these indications, go back and check everything. If necessary, power the Robot off and disconnect all connections to the PCB except for the power connection. Unplug the motor driver module, the Bluetooth module, and the two ICs from the board (leaving only the Pololu voltage regulator and the Photon in place) and power on again. If the Photon powers up, then power off and insert the Bluetooth module and try again. If this works, the plug in the two ICs and try again. If this works, then plug in the motor driver module and try again. If this works, begin reconnecting the motors and the ultrasonic sensors, one at a time to the PCB and keep trying until everything is connected and the PCB is correctly powering up.

If the Photon is new and has not yet been captured to your Particle account, follow Particle’s instructions here:

https://docs.particle.io/quickstart/photon/

The Robot is now fully assembled and powers up correctly. The next step is to install the Robot firmware onto the Particle Photon on the Robot PCB.

4.FIRMWARE INSTALLATION INSTRUCTIONS.

Firmware is the program (software) that you need to install on your Photon. The firmware for this project is provided in the form of source code. You will need to compile the source code and then “flash” it to your Photon.

Before you can perform any of these steps, you need to get your Photon working on your WiFi network and claimed into your Particle account. If you don’t have a Particle account, you need to create one (it’s free). Particle provides complete documentation for this. Begin at:

https://docs.particle.io/quickstart/photon/

You can perform these steps either by removing the Photon from the Robot PCB and powering it directly using a USB cable (as shown in Particle’s on-line documentation) or by performing these steps with the Photon in place in the installed project from section 3. We recommend that, however you do this, you do it in a location with a strong WiFi signal and in a place where you can observe the multi-color LED on the Photon.

If you are not familiar with Particle’s various integrated development environments, you can read up on the Web IDE and the Particle Workbench at:

https://docs.particle.io/tutorials/developer-tools/build/

The source file for the firmware for this project can be found at:

https://github.com/TeamPracticalProjects/Robotics/blob/master/Software/Firmware/AutonomousRobotParticle/src/AutonomousRobotParticle.ino (https://github.com/TeamPracticalProjects/Robotics/blob/master/Software/Firmware/AutonomousRobotParticle/src/AutonomousRobotParticle.ino)

This file is in Arduino source code format, which is just plain text and can be edited with any text editor or with either of Particle’s two supported integrated development environments (IDEs). If you are a novice Particle user, we suggest that you use the Web IDE. If you are familiar with the Particle Workbench, you may alternatively use it.

In order to install the Robot firmware on your Photon, you will need to compile and flash the file “AutonomousRobotParticle.ino” onto your Photon There are two ways to do this:

- Use the Particle Web IDE: Open a new project in the Web IDE and delete the default setup() and loop() templates. Open the file “AutonomousRobotParticle.ino” in this repository with any text editor or word processor program¹
. Now copy everything in the program and paste it into the blank template in the Web IDE. Be sure that all lines of “AutonomousRobotParticle.ino” are copied into the Web IDE window and save the program using any name that you wish. Next, use the Web IDE to select your target Photon and flash the code to it. For more information about the Particle Web IDE, see:

https://docs.particle.io/tutorials/developer-tools/build/

- Use the Particle Workbench: Copy the folder:

https://github.com/TeamPracticalProjects/Robotics/tree/master/Software/Firmware/Autonom ousRobotParticle (https://github.com/TeamPracticalProjects/Robotics/tree/master/Software/Firmware/AutonomousRobotParticle)

onto the computer where you are running the Particle Workbench. Open the file: AutonomousRobotParticle.code-workspace. Use Workbench to compile and flash this code to your Photon. For more information about the Particle Workbench, see:

https://docs.particle.io/tutorials/developer-tools/workbench/

The Web IDE approach is probably easier for someone who is new to Particle firmware development, as it is all web based. However, if you plan to develop firmware for Particle devices, we recommend that you install and learn the Workbench.

If you removed the Photon from the Robot PCB, now is the time to unpower it and place it back into the Robot PCB in your project. Power up the project and make sure that the Photon comes up with the multicolor LED breathing white.

NOTE: The Robot firmware places the Photon into “semi-automatic” mode. After flashing this firmware to the Photon, you will need to follow this procedure in order to re-flash firmware to the Photon again:

- Hold down both buttons on the Photon.
- Release the Reset button while continuing to hold down the Setup button.
- When the tricolor led blinks magenta release the Setup button.
- The multifunction LED on the Photon should flash green for a little while and then eventually “breathe magenta” continuously. This is “safe mode” and the Photon is now

1 When using a word processing program for this purpose, be sure that it is in plain text mode.

connected to the Particle Cloud and not running any local firmware. You can now flash new firmware to your Photon. See the Particle documentation for more information: https://docs.particle.io/tutorials/device-os/led/photon/

5.ROBOT APP INSTALLATION INSTRUCTIONS.

This project includes an Android app. This App allows the user to control and monitor the Robot. We have provided both source code and an installation file for this App. Source code (in MIT App Inventor 2 source file format) can be found at:

https://github.com/TeamPracticalProjects/Robotics/blob/master/Software/AI2_app/src/BasicRob otControl.aia (https://github.com/TeamPracticalProjects/Robotics/blob/master/Software/AI2_app/src/BasicRobotControl.aia)

You need this file only if you want to view and/or modify the app.

The installation file can be found at:

https://github.com/TeamPracticalProjects/Robotics/blob/master/Software/AI2_app/compiled/Bas icRobotControl.apk (https://github.com/TeamPracticalProjects/Robotics/blob/master/Software/AI2_app/compiled/BasicRobotControl.apk)

The installation file is called BasicRobotControl.apk.

In order to install this app on your Android device, you must transfer this installation file to your device. There are several ways to do this; here are three suggestions:

- Downloading: Download the file BasicRobotControl.apk to your Android device using a web browser on the device. Make sure that you know the folder on the Android device where the browser stores downloaded files.
- Sideloading: Download the file BasicRobotControl.apk to your desktop or laptop computer. Attach a USB cable from your desktop/laptop to your Android device. The Android device’s flash memory should appear as a drive on your computer. Drag and drop the installation file to a location on the Android device where you will be able to find it later.
- E-mail: Download the file BasicRobotControl.apk to your desktop or laptop computer. Email this file to yourself as an attachment. Open email on your Android device and download the attachment, making sure that you know where the email program/browser stores attachments.

Regardless of the method that you use to get the file BasicRobotControl.apk onto your Android device, you now use a file explorer on your device to locate the file and tap on it to start the installation. The App should now install on your Android device. NOTE: you may get a message on your Android device saying that the App is “untrusted” or “unverified”. This means that Android knows that the App did not come from the Google play store. Go ahead and install it anyway – it is safe! The installer will list the permissions that the App needs to run. Go ahead and accept them. The App should install properly.

Once the App is installed on your Android device, tap on its icon to open it. You should see a screen similar to figure 6-1.

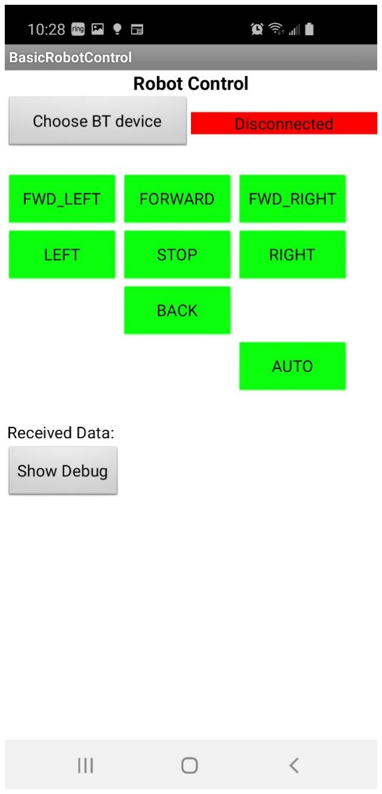
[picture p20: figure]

Figure 6-1. App Main Screen.

You are now ready to operate your Robot. Refer to the User manual “Robot_User_Manual.pdf” for instructions about operating your Robot. It can be found in the following folder:

https://github.com/TeamPracticalProjects/Robotics/tree/master/Documents

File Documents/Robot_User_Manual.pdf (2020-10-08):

# Robot User Manual

By: Jim Schrempp and Bob Glicksman; v2, 10/8/2020


© 2020 Team Practical Projects, Bob Glicksman and Jim Schrempp. All rights reserved.

NOTICE: Use of this document is subject to the terms of use described in the document
“Terms_of_Use_License_and_Disclaimer ” that is included in this release package. This document can be found at:

https://github.com/TeamPracticalProjects/Robotics/blob/master/Terms_of_Use_License_and_Disclaimer.pdf

© 2020, Team Practical Projects, Jim Schrempp AND Bob Glicksman; all rights reserved. Subject to “Terms of Use, License and Disclosure”

TABLE OF CONTENTS.

TABLE OF CONTENTS. | 1
1. | OVERVIEW. | 2
2. | ROBOT COMPONENTS UNDER USER CONTROL. | 2
3. | ROBOT APP USER INSTRUCTIONS. | 4

1.OVERVIEW.

This document describes how to control your Robot. In order to run your Robot, you must have completed all of the steps in the document “Robot_Build_and Installation_Instructions.pdf” that is located in this folder. These steps include:

- Building and testing the Robot PCB.
- Assembling and wiring the Robot.
- Installing the Robot Firmware on the Particle Photon microcontroller module located on the Robot PCB.
- Installing the Robot App on an Android phone or tablet.

The Robot has two switches that the user can control. These are described in section 2 of this document. Once the Robot is turned on and the motors enabled, the Robot is controlled through an Android app. The Robot App is described in section 3 of this document.

# 2.ROBOT COMPONENTS UNDER USER

CONTROL.

The Robot has two switches that the User can access; see figure 2-1.

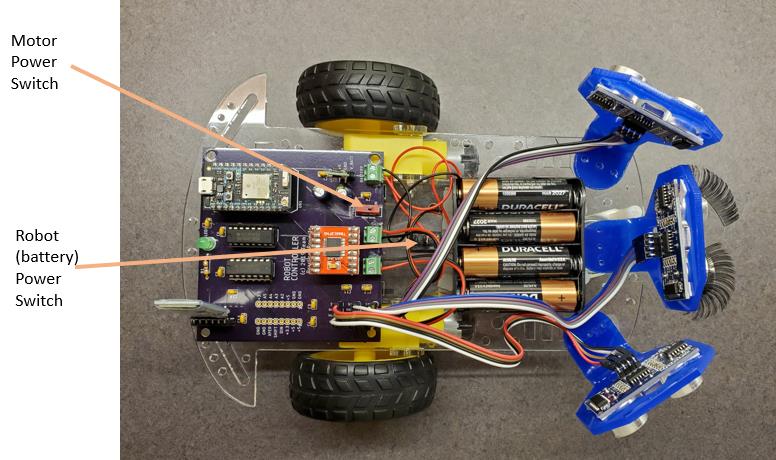
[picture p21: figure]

Figure 2-1. Switches on the Robot.

The “motor power switch” is a slide switch that is mounted on the Robot PCB. This is a 2 position slide switch. Normally, this switch is set forward, i.e. toward the batteries, as shown in the closeup view of figure 2-2. In this position, the Robot electronics can control the drive wheel motors. If the “motor power switch” is set to the rear of the Robot, the Robot electronics will perform normally but the motors will be de-energized. This latter position of the “motor power switch” is available for testing and debugging purposes only. In normal use, this switch should be set in the forward position (per figure 2-2) so that the motors are energized.

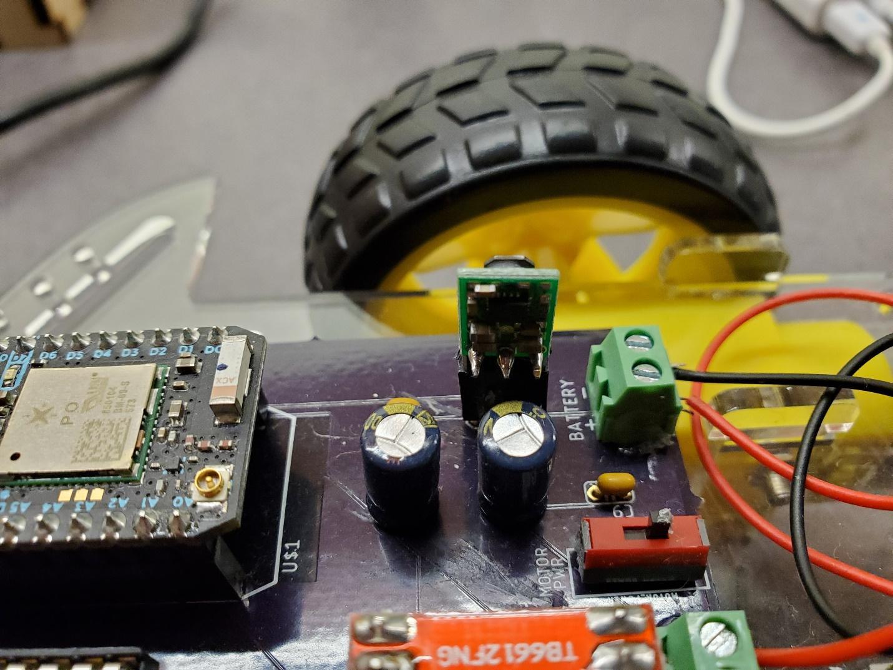
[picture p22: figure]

Figure 2-2. Motor Power Switch Closeup (normal position).

The “battery power switch” is located between the PCB and the batteries. This is a rocker switch and the switch control is on the underside of the Robot, as shown in figure 2-3. In the “0” position, the batteries are disconnected and the Robot is completely powered off. In the “1” position, the batteries are connected to the electronics and the Robot can function. We suggest that you turn this switch off whenever you are not actively using the Robot, in order to conserve the batteries. Turn this switch ON (to “1”) whenever you want to use your Robot.

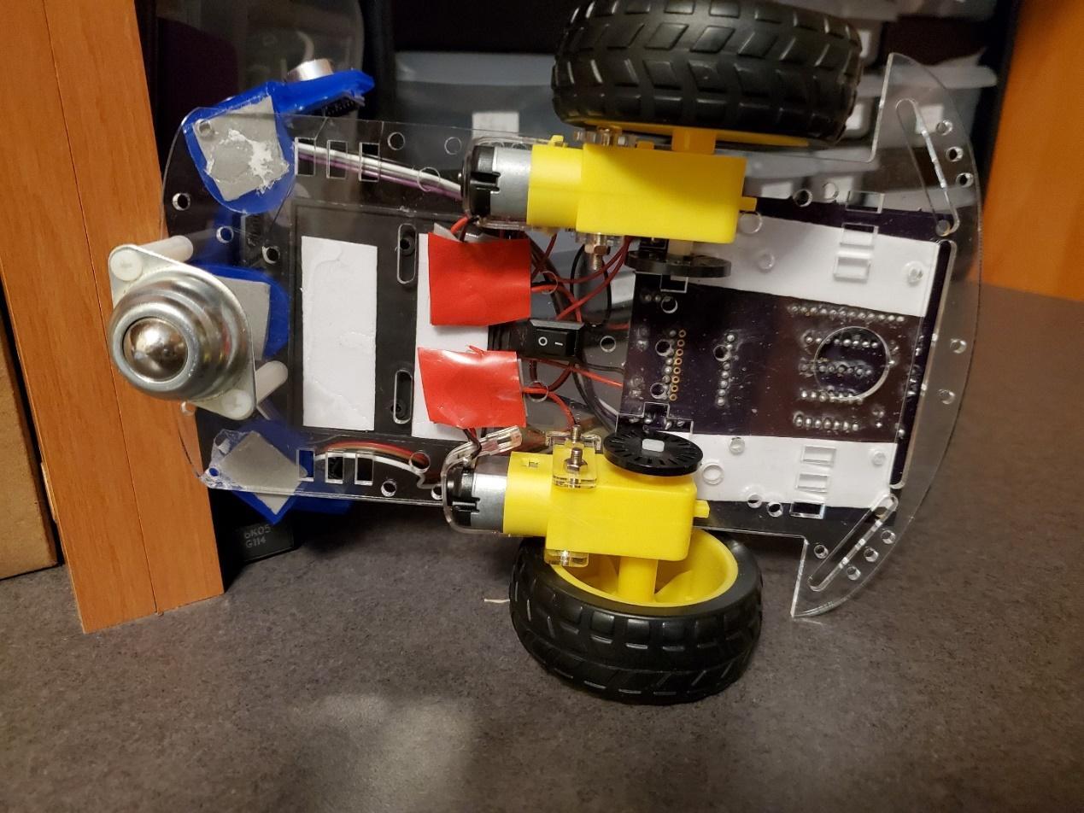
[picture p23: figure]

Figure 2-3. Battery Power Switch.

3.ROBOT APP USER INSTRUCTIONS.

When you open the Robot App on your Android device, you should see a screen similar to figure 3-1, below. Note the word “Disconnected” in red at the top right of the screen. This indicates that you must first create a Bluetooth connection between the App and your Robot. If you look at the Bluetooth module on your Robot, you will see a flashing red LED. This also indicates that the Robot’s Bluetooth module is not connected to any device at this time.

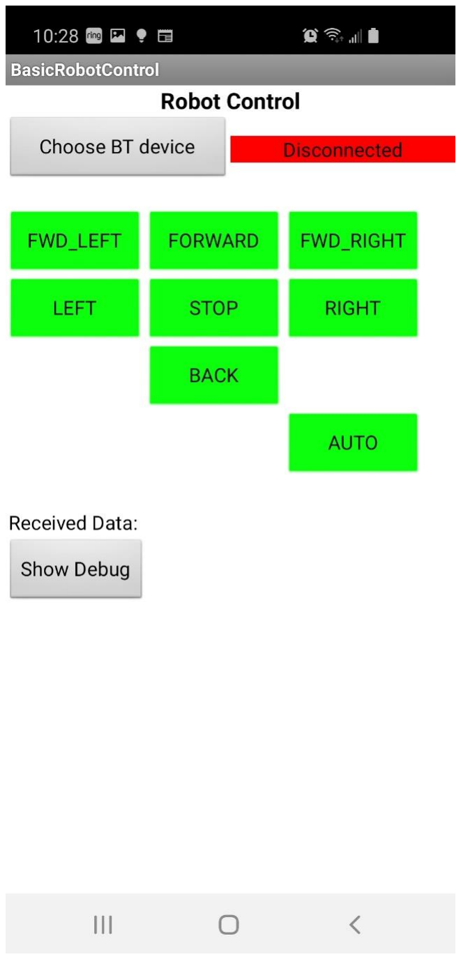
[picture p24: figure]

Figure 3-1. App Opening Screen.

Make sure that the Robot is powered on and is nearby to you. Now, tap in the “Choose BT device” button at the top left side of the App screen. You will now see a screen similar to figure 3-2. Note that there will be some long coded numbers (MAC Addresses) in the fields that are blanked out in red in figure 3-2.

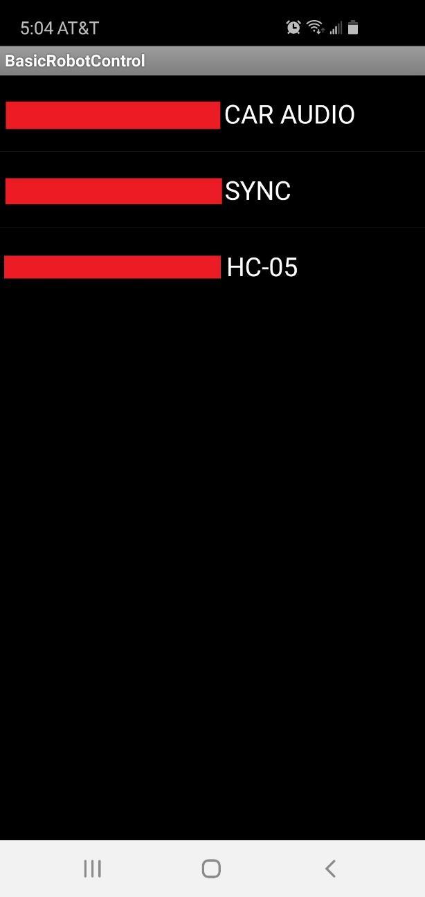
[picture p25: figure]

Figure 3-2. Bluetooth Connection Selector Screen.

Locate your device on the screen in figure 3-2. It should say “HC-05”¹
. Tap on this device to
make the Bluetooth connection between your App and the Robot. At this time, you should see two things change:
- The App should return to the main screen with the top right message now saying “Connected” in a gray field; see figure 3-3.

1
If you do not see your Robot’s HC-05 module on this list, then you need to “pair” your Android device with the HC-05 module. Go to your Android device’s “Settings” and find the Bluetooth settings. Use this screen to find all Bluetooth devices in range and then select the HC-05 device and follow the instructions on your Android device to “pair” with it. Once your Robot’s HC-05 is paired with your Android device, you should be able to use these instructions to connect with it without having the pair again.

- The red LED on the Bluetooth module on the Robot should now just occasionally flash red, as opposed to flashing red continuously. This verifies that the App is now communicating with the Robot.

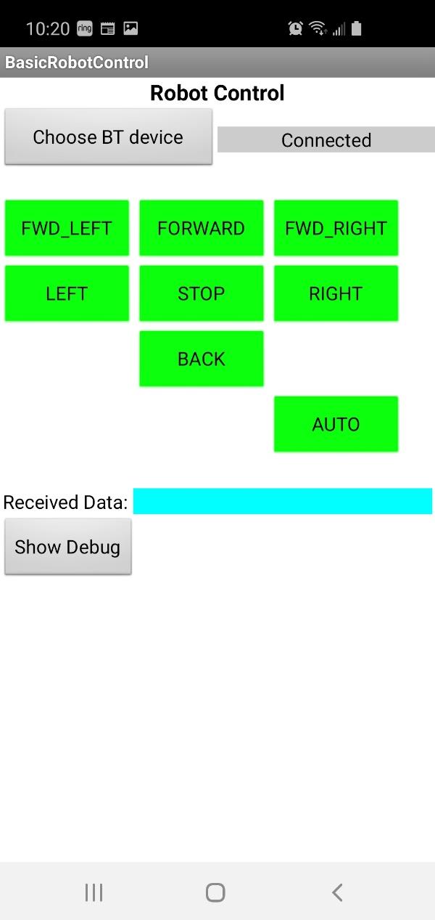
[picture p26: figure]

Figure 3-3. Robot Bluetooth Connected.

At this point, you are ready to use the App to control your Robot. There are two modes of Robot control: manual and automatic. In “manual” mode, you can use the green buttons on the App to manually control the Robot, as follows:

- STOP button: tapping this button brakes the Robot to stop it. The Robot remains stopped until you tap another button. The green LED on the back of the Robot PCB is off when the Robot is stopped.
- FORWARD button: tapping this button moves the Robot forward at high speed. The Robot continues until you tap STOP or any other of the buttons. The green LED on the back of the Robot PCB is on when the Robot is moving.
- BACK button: tapping this button moves the Robot backward at high speed. The Robot continues until you tap STOP or any other of the buttons. The green LED on the back of the Robot PCB is on when the Robot is moving.
- LEFT button: tapping this button causes the Robot to pivot to the left. The Robot continues pivoting until you tap STOP or any other of the buttons. The green LED on the back of the Robot PCB is on when the Robot is moving.
- RIGHT button: tapping this button causes the Robot to pivot to the right. The Robot continues pivoting until you tap STOP or any other of the buttons. The green LED on the back of the Robot PCB is on when the Robot is moving.
- FWD_LEFT button: tapping this button causes the Robot to move forward while turning left, at medium speed. The green LED on the back of the Robot PCB is on when the Robot is moving.
- FWD_RIGHT button: tapping this button causes the Robot to move forward while turning right, at medium speed. The green LED on the back of the Robot PCB is on when the Robot is moving.
- AUTO: this button places the Robot into automatic navigation mode, which is described further below. The Robot remains in automatic mode until some other button is tapped. The green LED on the back of the Robot PCB is on when the Robot is moving.

Note that after tapping any button, the button color turns to yellow and remains so until some other button is tapped. A yellow button indicates the active control on the Robot.

Figure 3-4 is a photo of the App after placing the Robot into automatic navigation (AUTO) mode. When the Robot is in AUTO mode, it uses the three ultrasonic sensors to navigate automatically, avoiding collisions with obstacles in its path.

When the Robot is in AUTO mode, the App displays some additional information below the buttons, as illustrated in figure 3-4. This additional information indicates the Robot’s current action. The following is brief description of how the Robot navigates when in AUTO mode.

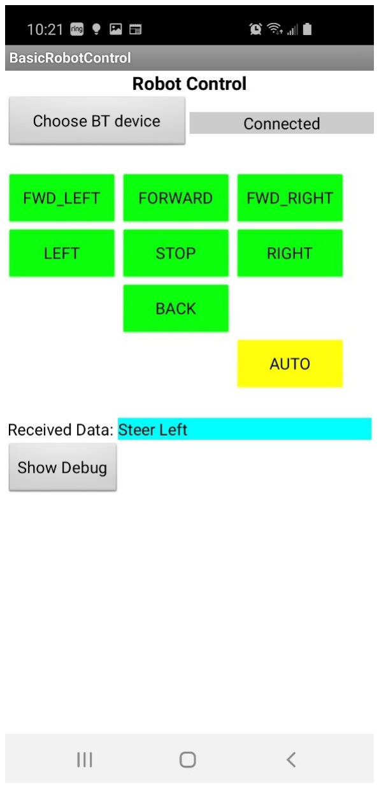
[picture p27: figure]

Figure 3-4. Robot Automatic Navigation Mode.

When the Robot is in AUTO mode, it primarily uses the front ultrasonic sensor to detect obstacles. If the front ultrasonic sensor detects an obstacle ahead, it randomly selects a direction to pivot (left or right) and it pivots in that direction until it finds an open space ahead. The Robot should always find an open space ahead; at the very least, it pivots 180 degrees so that “ahead” is now the path that the robot came in on. If this path is blocked and the Robot can’t find an open space anywhere, it automatically exits the AUTO mode and stops.

The two side sensors are needed for the Robot to detect that it is angling toward a wall or other obstacle; i.e. the obstacle is not directly ahead but the Robot is approaching it at an oblique angle. When one of these sensors detects that the Robot is too close to a side obstacle, the Robot pivots away from it until it is clear on the sides. If the Robot detects that it is too close to both sides (i.e. the corridor narrows, the Robot backs up until it is clear enough on one side to pivot around and exit the way it came in.

The App has an additional button – a gray button that says “Show Debug”. Tapping this button causes the App to display a history of the Robot’s decision messages, along with the distance readings that caused the Robot to make an AUTO mode decision. See figure 3-5, below.

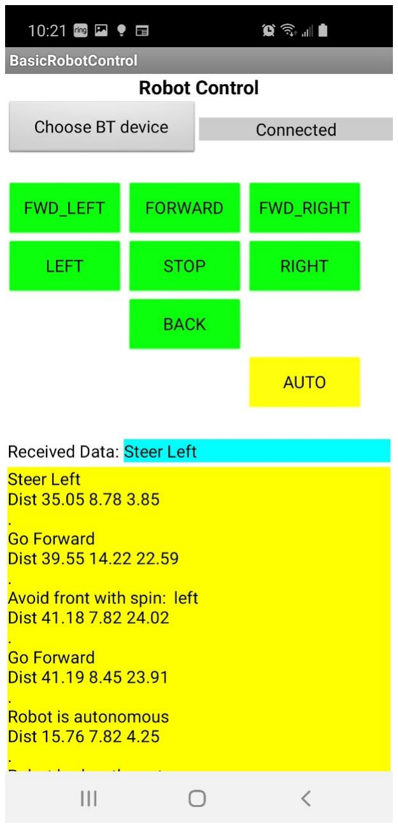
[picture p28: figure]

Figure 3-5. Auto Mode with Debug Log.

This extra information is normally not used but it can be useful in understanding how the Robot got into some situation and how it responded to that situation. The Robot firmware publishes an entry for this log display every time that it makes a new AUTO mode decision, e.g. stop going forward and steer to the left. Each log entry contains the Robot’s new decision and, just below this decision, displays the three distance measurements that drove the decision. For example, the entry:

Steer Left

Dist 35.05 8.78 3.85

Means the following:

- The Robot decided that it needs to steer to the left (turn left while moving forward at low speed)
- The basis for this decision was:
- Ultrasonic left side measurement is 35.05 inches, which is clear to the left.
- Ultrasonic front measurement is 8.78 inches, which still has room to move forward.
- Ultrasonic right side measurement is 3.85 inches, which is too close on the right.

Since the Robot must get clear of the right side and it has room to move forward, the decision is to “steer left” (as opposed to “swivel left”, where the Robot pivots and does not move forward while doing so).

The log is read from the top down, where the most recent entry is at the top, the next entry down is the Robot’s previous decision, etc.

When you are through using your Robot, you may close the App on your Android device. We recommend that you turn off the Robot power using the battery power switch on the underside of the Robot when it is not in use. This will extend the life of the batteries that power the Robot.

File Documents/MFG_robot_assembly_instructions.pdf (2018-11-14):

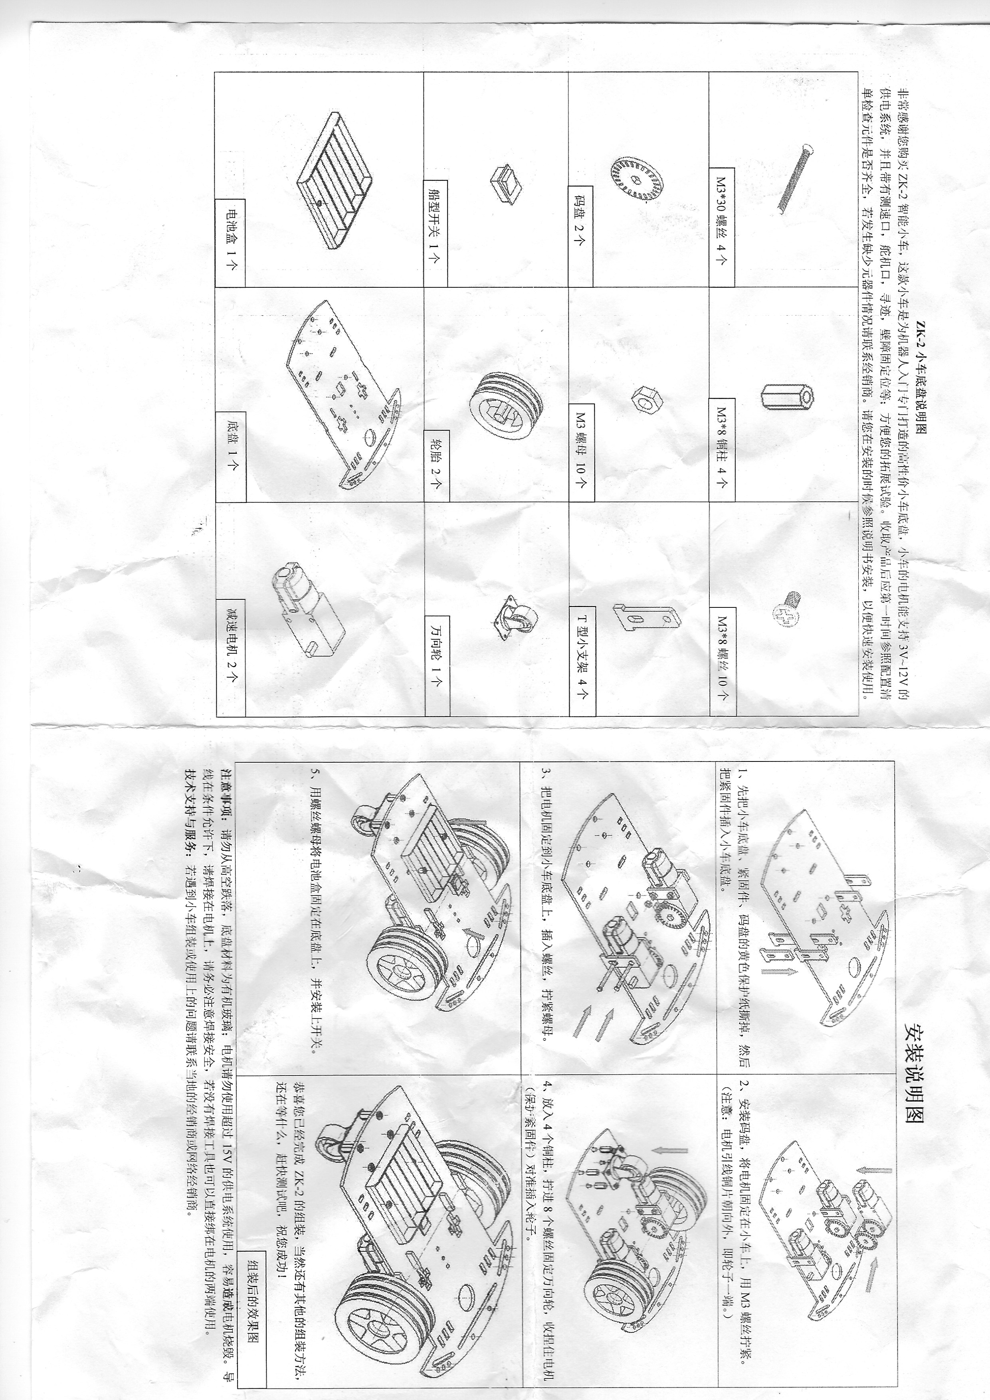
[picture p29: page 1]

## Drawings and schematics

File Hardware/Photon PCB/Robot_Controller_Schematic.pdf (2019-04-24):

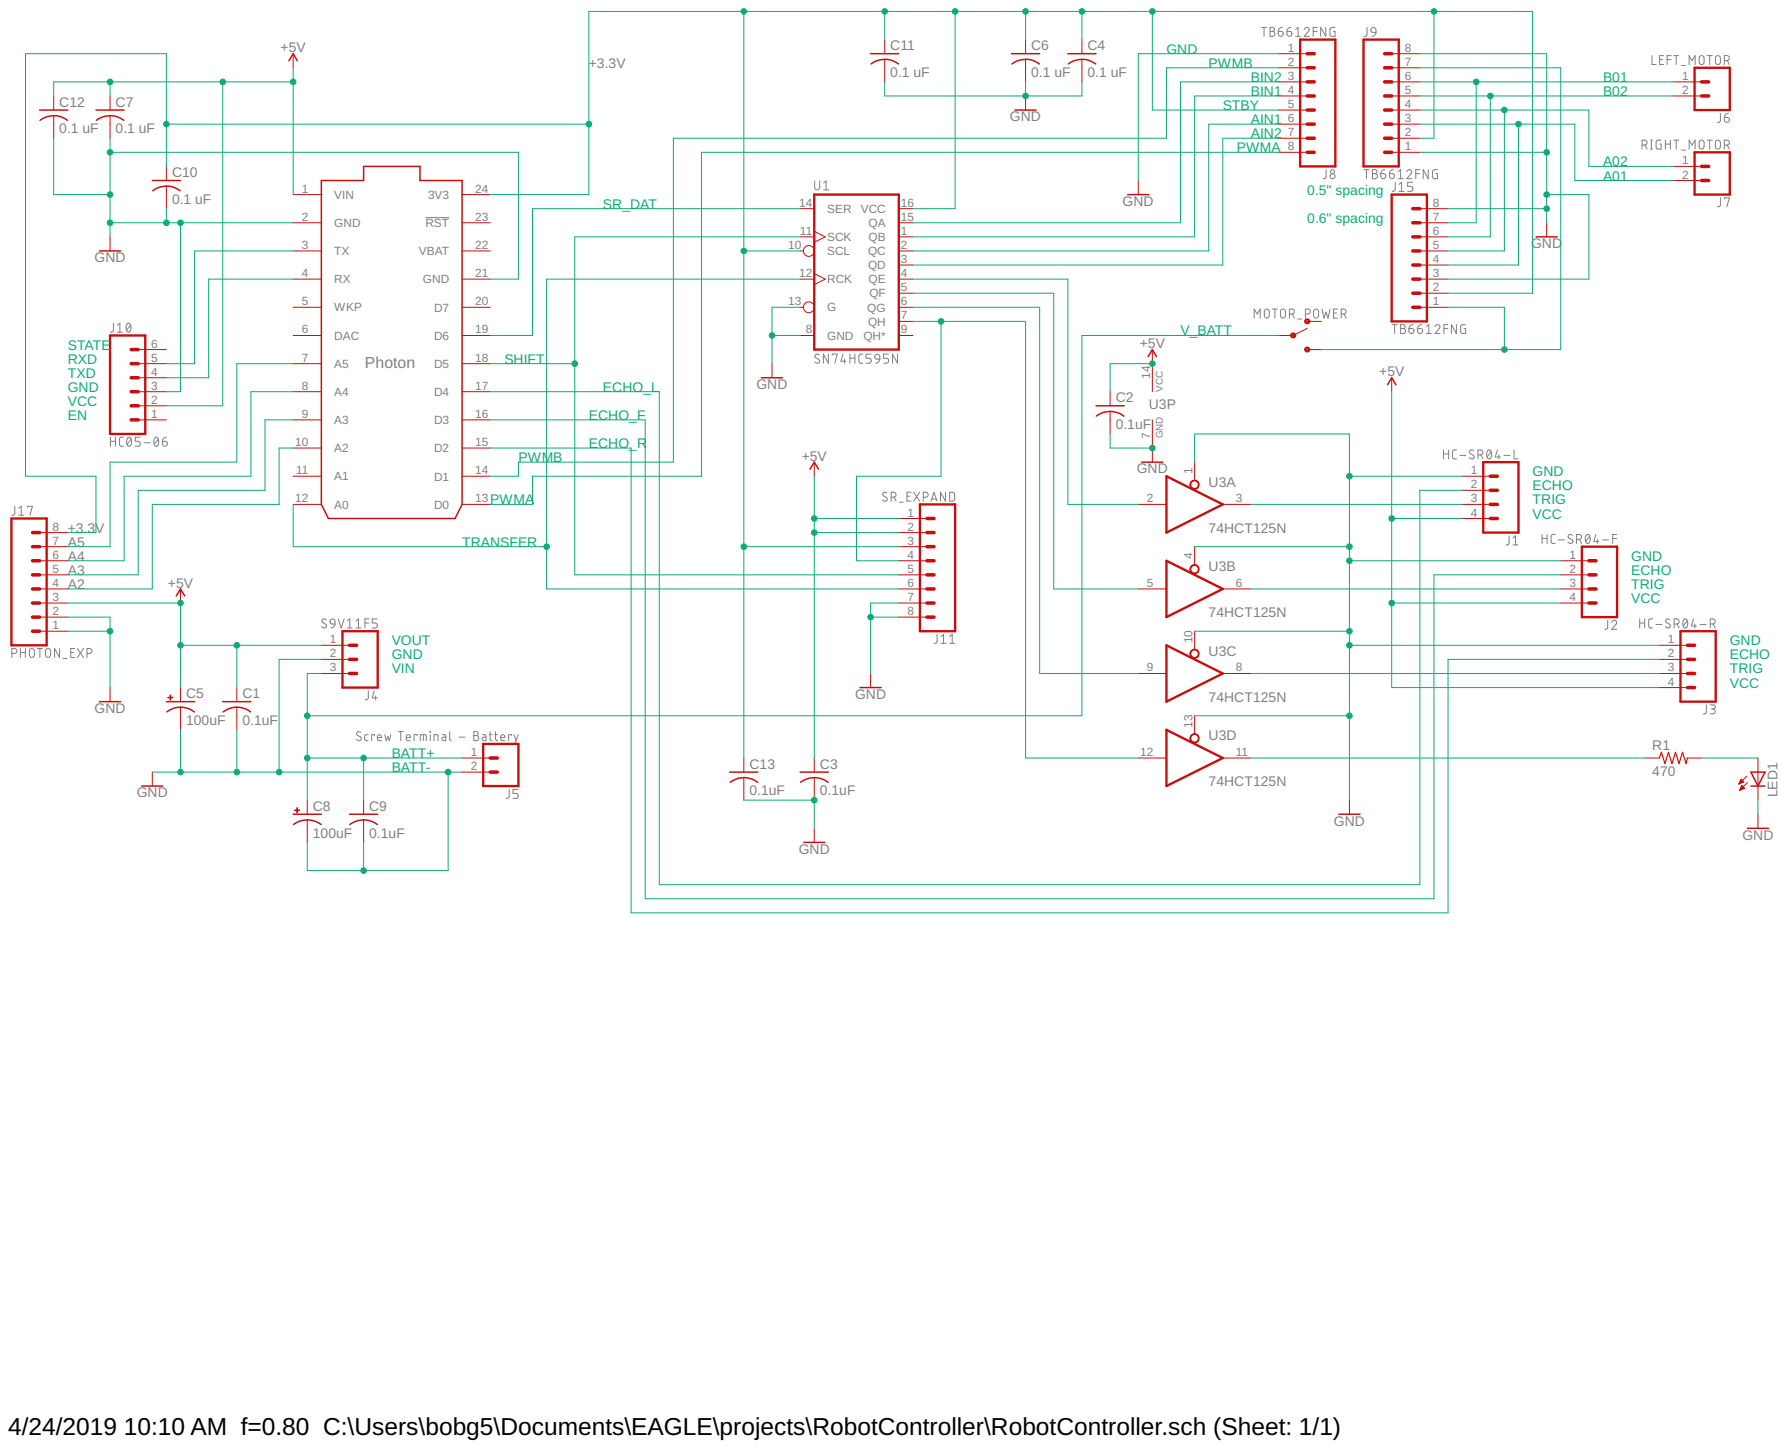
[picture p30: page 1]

6 5 4

15 D1 PWMB

4/24/2019 10:10 AM f=0.80 C:\Users\bobg5\Documents\EAGLE\projects\RobotController\RobotController.sch (Sheet: 1/1)

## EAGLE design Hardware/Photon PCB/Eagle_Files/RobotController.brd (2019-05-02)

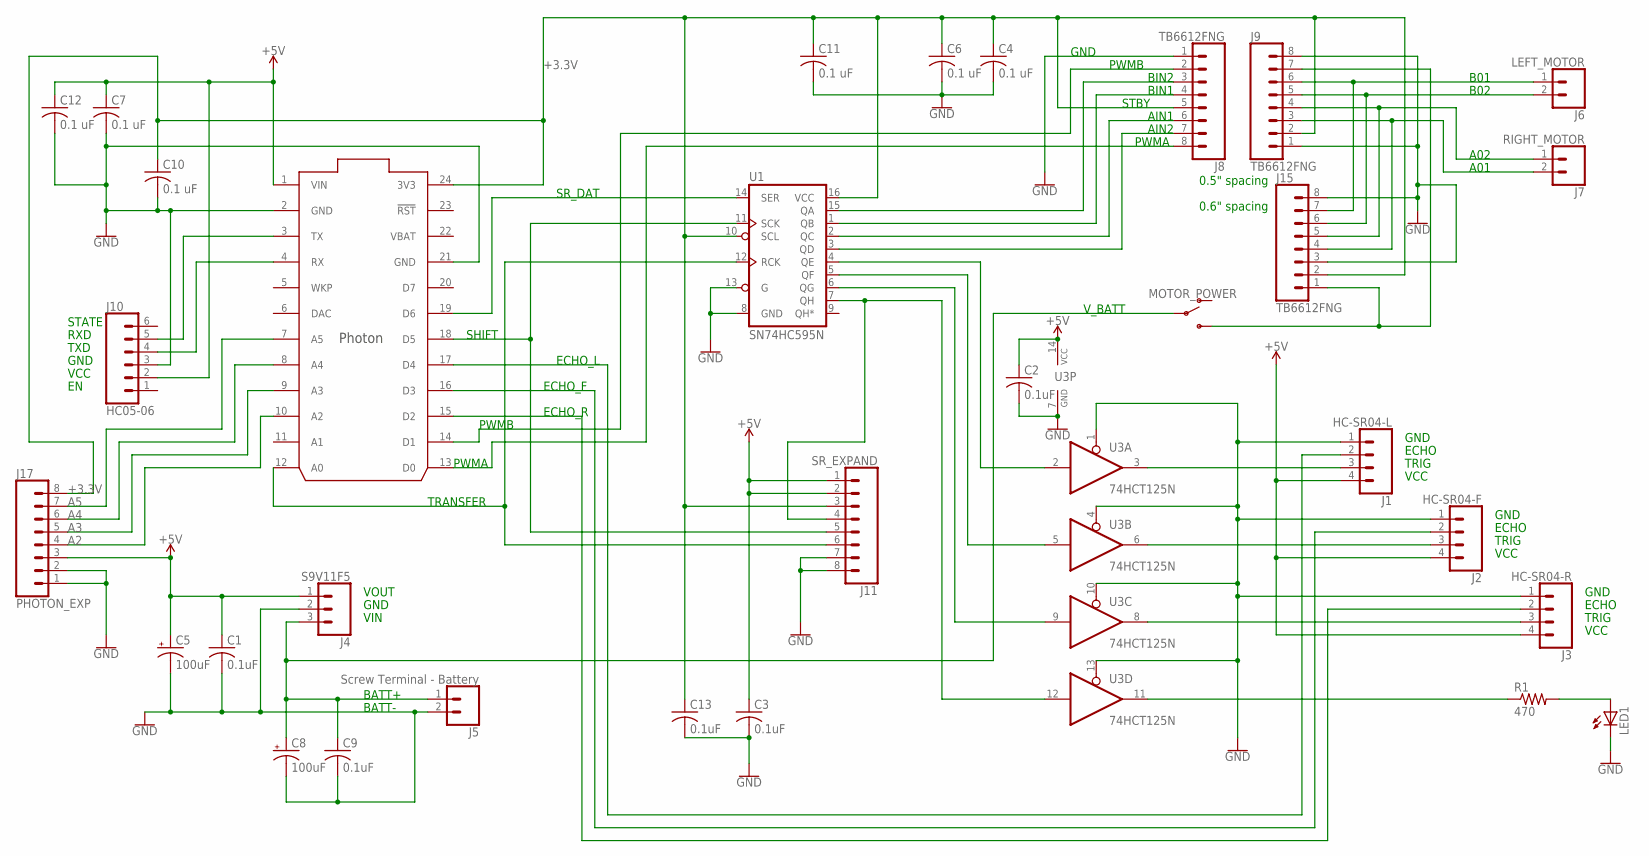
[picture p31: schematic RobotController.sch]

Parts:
C1, C2, C3, C9, C13: 0.1uF; C025-024X044
C4, C6, C7, C10, C11, C12: 0.1 uF; C025-024X044
C5, C8: 100uF; E2,5-6E
J1: HC-SR04-L; 1X04
J2: HC-SR04-F; 1X04
J3: HC-SR04-R; 1X04
J4: S9V11F5; 1X03
J5: Screw Terminal - Battery; SCREWTERMINAL-3.5MM-2
J6: LEFT_MOTOR; SCREWTERMINAL-3.5MM-2
J7: RIGHT_MOTOR; SCREWTERMINAL-3.5MM-2
J8, J9, J15: TB6612FNG; 1X08
J10: HC05-06; 1X06
J11: SR_EXPAND; 1X08
J17: PHOTON_EXP; 1X08
LED1: LED5MM
MOTOR_POWER: SWITCH-SPDT-PTH-11.6X4.0MM; SWITCH_SPDT_PTH_11.6X4.0MM
R1: 470; 0207/10
U1: SN74HC595N; DIP16
U3: 74HCT125N; DIL14
U$1: PHOTON_WITH_HEADERS; PHOTON

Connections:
+3.3V: C4.1, C6.1, C10.1, C11.1, C13.1, J8.5, J9.2, J11.3, J15.2, J17.8, U1.10 (SCL), U1.16 (VCC), U$1.24 (3V3)
A2: J17.4, U$1.10 (A2)
A3: J17.5, U$1.9 (A3)
A4: J17.6, U$1.8 (A4)
A5: J17.7, U$1.7 (A5)
GND: C1.2, C2.2, C3.2, C4.2, C5.-, C6.2, C7.2, C8.-, C9.2, C10.2, C11.2, C12.2, C13.2, J1.1, J2.1, J3.1, J4.2, J5.2, J8.1, J9.1, J9.8, J10.3, J11.7, J11.8, J15.3, J15.8, J17.1, J17.2, LED1.K (C), U1.8 (GND), U1.13 (G), U3.1 (OE), U3.4 (OE), U3.7 (GND), U3.10 (OE), U3.13 (OE), U$1.2 (GND), U$1.21 (GND)
unnamed: U1.14 (SER), U$1.19 (D6)
unnamed: J11.6, U1.12 (RCK), U$1.12 (A0)
unnamed: J11.4, U1.7 (QH), U3.12 (I)
unnamed: U1.4 (QE), U3.2 (I)
unnamed: U1.5 (QF), U3.5 (I)
unnamed: U1.6 (QG), U3.9 (I)
unnamed: J9.7, J15.1, MOTOR_POWER.3 (S)
unnamed: J11.5, U1.11 (SCK), U$1.18 (D5)
unnamed: C8.+, C9.1, J4.3, J5.1, MOTOR_POWER.2
unnamed: J1.3, U3.3 (O)
unnamed: J2.3, U3.6 (O)
unnamed: J3.3, U3.8 (O)
unnamed: R1.1, U3.11 (O)
unnamed: LED1.A, R1.2
unnamed: J7.2, J9.3, J15.4
unnamed: J7.1, J9.4, J15.5
unnamed: J6.2, J9.5, J15.6
unnamed: J6.1, J9.6, J15.7
unnamed: J2.2, U$1.16 (D3)
unnamed: J8.3, U1.15 (QA)
unnamed: J3.2, U$1.15 (D2)
unnamed: J8.4, U1.1 (QB)
unnamed: J8.6, U1.2 (QC)
unnamed: J8.7, U1.3 (QD)
unnamed: J1.2, U$1.17 (D4)
unnamed: J8.2, U$1.14 (D1)
unnamed: J8.8, U$1.13 (D0)
unnamed: J10.5, U$1.3 (TX)
unnamed: J10.4, U$1.4 (RX)
VBAT: U$1.22 (VBAT)
VCC: C1.1, C2.1, C3.1, C5.+, C7.1, C12.1, J1.4, J2.4, J3.4, J4.1, J10.2, J11.1, J11.2, J17.3, U3.14 (VCC), U$1.1 (VIN)

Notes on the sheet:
VIN
GND
VOUT
BATT+
BATT-
ECHO
TRIG
VCC
V_BATT
PWMA
PWMB
STBY
BIN1
BIN2
AIN2
AIN1
B01
B02
A02
A01
0.5" spacing
SHIFT
TRANSFER
SR_DAT
ECHO_L
ECHO_F
ECHO_R
TXD
RXD
STATE
0.6" spacing

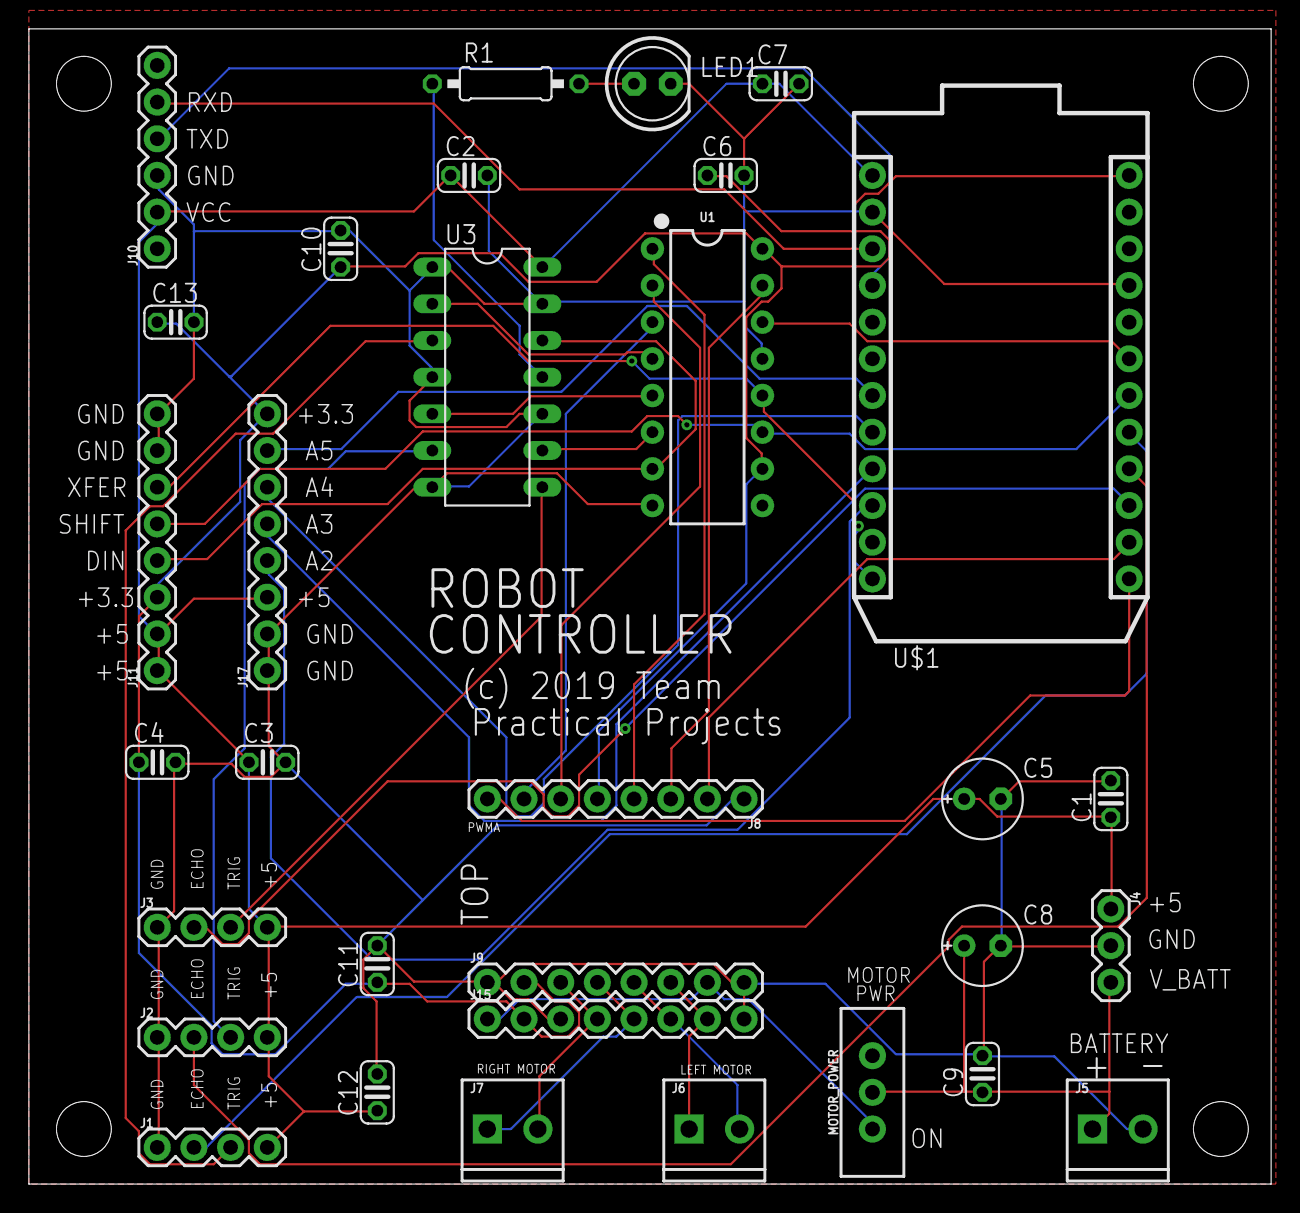
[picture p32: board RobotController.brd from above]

Board: 2 copper layers, 86.0 x 80.0 mm, 32 parts (0 on the bottom side), 36 nets.

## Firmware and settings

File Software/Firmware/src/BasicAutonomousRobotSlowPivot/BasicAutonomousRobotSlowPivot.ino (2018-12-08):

/* Basic Autonomous Robot: The robot can be controlled manually via an app (Basic Robot Movement) and can also be placed
 *  into autonomous mode.  When in autonomous mode, the robot uses the HC-SR04 ultrasonic range finder to detect an
 *  obsticle in front. If forward movement is obstructed, the robot pivots and measures to find an open path ahead and then
 *  continues forward on that path until again obstructed or commanded out of the autonomous mode.  The robot delares that it is
 *  stuck if it cannot find an open path within a predetermined number of pivots/distance measurements.  If the robot is stuck 
 *  in this manner, it automatically exits autonomous mode and must be commanded manually again via the app.
 *  
 *  This version of the robot has one ultrasonic rangefinder mounted on a servo at the front of the robot.  The servo
 *  is ONLY used to position the ultrasonic sensor dead forward.  It has been decided that two more ultrasonic rangefinders will
 *  be added to the sides of the robot.  These sensors will be used (in a future version of this firmware) to detect if the robot
 *  is too close to a wall along the side and will stear the robot away accordingly.  In this version, side wall hit detection
 *  is NOT implemented.
 *  
 *  by: Bob Glicksman, Team Practical Projects
 *  version 1.1
 *  12/08/2018
*/

//#define DEBUG   // uncomment this line to use serial monitor for debugging

// libraries to include
#include "Arduino.h"
#include <SoftwareSerial.h>
#include <Servo.h>

// Global constants
  // motor speeds
const int HIGH_SPEED = 200;
const int LOW_SPEED = 150;
const int SLOW_SPEED = 100; // for tight turns while seeking open space

  // pivot time for searching
const int PIVOT_TIME = 400; // time in milliseconds to pivot robot while searching

  // ultrasonic scan and measurement times
const int SERVO_FRONT_OFFSET = -5;  // offset to achieve mechanical position of front for angle = 90; your servo may vary.
const int FRONT_MEASURE_ANGLE = 90; // front
const float OBSTRUCTION_CLOSE_DISTANCE = 8.0; // distance (inches) that is too close; must stop and turn
const float CLEAR_AHEAD = 18; // minimum distance (inches) for robot to be OK to move ahead

  // robot command modes from app
const int NO_COMMAND = -1;
const int MANUAL = 0;
const int AUTO = 1;

// Pins
  // sero and ultrasonic rangefined pins
const int SERVO_PIN = A0;  // servo wiring: attach red wire to Vcc; brown wire to ground; yellow wire to Arduino pin A0
const int TRIG_PIN = A1;
const int ECHO_PIN = A2;

  // Motor A control pins
const int PWMA = 11;
const int AIN1 = 12;
const int AIN2 = 7;
const int MOTORA = 0;

  // Motor B control pins
const int PWMB = 5;
const int BIN1 = 2;
const int BIN2 = 3;
const int MOTORB = 1;

  // bluetooth serial pins
const int BT_RX = 10; // received serial data from the bluetooth module Tx pin
const int BT_TX = 6;  // transmitted data to the bluetooth mosule Rx pint (through a voltage divider)

  // LED pin
const int LEDpin = 8;

// Global variables
SoftwareSerial BTserial(BT_RX, BT_TX);  // instance of SoftwareSerial to communicate with the bluetooth module
Servo sweepServo;  // instance of Servo object to control the untrasonic sweep sero

/**************************************************************************
 *  setup() 
***************************************************************************/
void setup() {
    // motor control pins
  pinMode(PWMA, OUTPUT);
  pinMode(AIN1, OUTPUT);
  pinMode(AIN2, OUTPUT);
  
  pinMode(PWMB, OUTPUT);
  pinMode(BIN1, OUTPUT);
  pinMode(BIN2, OUTPUT);

    // LED output pin
  pinMode(LEDpin, OUTPUT);

  // Set the baud rate of the bluetooth module
  BTserial.begin(9600);
 
  // instantiate the sweep servo
  sweepServo.attach(SERVO_PIN);

  // set up ultrasound module pins
  pinMode(TRIG_PIN, OUTPUT); 
  pinMode(ECHO_PIN, INPUT);

  // make sure the robot is stopped
  robotStop();

  // center the servo
  sweepServo.write(90 + SERVO_FRONT_OFFSET);

  // flash the LED twice to indicate setup is complete
  for(int i = 0; i < 2; i++) {
    digitalWrite(LEDpin, HIGH);
    delay(500); 
    digitalWrite(LEDpin, LOW);
    delay(500);
  }

#ifdef DEBUG
  // Setup serial monitor communication for use in debugging
  Serial.begin(9600);
  Serial.println("Set up complete");
#endif  

}  // end of setup()

/**************************************************************************
 *  loop() 
***************************************************************************/
void loop() {
  
  static float frontDistance; // the measured distance ahead
  static int currentMode = MANUAL;  // place in manual mode until commanded otherwise
  int commandMode;

  commandMode = command(); // look for bluetooth command and process command accordingly
  switch (commandMode) {
    case (MANUAL):    // change the current mode to manual
      currentMode = MANUAL;
      break;
    case (AUTO):    // change the current mode to auto
      currentMode = AUTO;
      break;
    case (NO_COMMAND):  // leave current mode as it was
      break;
    default:    // leave current mode as it was
      break;
  }
  
#ifdef DEBUG
  Serial.print("mode: ");
  if(currentMode == MANUAL) Serial.println("manual"); else if (currentMode == AUTO) Serial.println("auto"); else Serial.println("undefined");
#endif

  // process automonomous mode
  if(currentMode == AUTO){
    frontDistance = measureDistance();  // take ultrasonic range measurement forward

#ifdef DEBUG
  Serial.print("measured forward distance: ");
  Serial.println(frontDistance);
#endif
  
    if(frontDistance < OBSTRUCTION_CLOSE_DISTANCE){ // we are too close, sweep the sides to find where clear
      int dir = random(2);  // random number between 0 (left) and 1(right)    
      if (scan(dir)) {   // scan; return true if OK to move forward, false if stuck
        robotForward(LOW_SPEED);  // it is clear ahead
      } else {    // we are stuck
        robotStop();
        digitalWrite(LEDpin, LOW);
        currentMode = MANUAL;
      }     
    } else {    // clear ahead so move forward
      robotForward(LOW_SPEED);  // it is clear ahead
    }
  }
  
} // end of loop()


/**************************************************************************
 *  Function to process bluetooth commands
***************************************************************************/
int command() { 
  static int mode = NO_COMMAND; 
  
  // Test if command character received by bluetooth
  if (BTserial.available() > 0) {

    // Get the char
    char data = (char) BTserial.read();

    // Control the robot according to the command
    switch (data) {

    case 'a': // place the robot in automatic mode. Any other button puts it back in manual mode
      digitalWrite(LEDpin, HIGH);
      robotStop();
#ifdef DEBUG
      Serial.println("robot is autonomous");
#endif      
      BTserial.print("Robot is autonomous");
      mode = AUTO;
      break;
      
    case 'f': // robot forward
      digitalWrite(LEDpin, HIGH);
      robotForward(HIGH_SPEED);
#ifdef DEBUG
      Serial.println("robot moves forward");
#endif
      BTserial.print("Robot moves forward");
      mode = MANUAL;
      break;

    case 'l':  // robot tight turn left at slow speed
      digitalWrite(LEDpin, HIGH);
      robotLeft(SLOW_SPEED);
#ifdef DEBUG
      Serial.println("robot pivots left");
#endif
      BTserial.print("Robot pivots left");
      mode = MANUAL;
      break;
      
    case 'r':  // robot tight turn right at slow speed
      digitalWrite(LEDpin, HIGH);
      robotRight(SLOW_SPEED);
#ifdef DEBUG
      Serial.println("robot piviots right");
#endif
      BTserial.print("Robot piviots right");
      mode = MANUAL;
      break;

    case 'b':  // robot moves backward at low speed
      digitalWrite(LEDpin, HIGH);
      robotBack(LOW_SPEED);;
#ifdef DEBUG
      Serial.println("robot moves backward");
#endif
      BTserial.print("Robot moves backward");
      mode = MANUAL;
      break;
      
    case 'w':  // robot turns leftward at low speed
      digitalWrite(LEDpin, HIGH);
      robotFwdLft(LOW_SPEED);
#ifdef DEBUG
      Serial.println("robot turns leftward");
#endif
      BTserial.print("Robot turns leftward");
      mode = MANUAL;
      break;

    case 'e':  // robot turns rightward at low speed
      digitalWrite(LEDpin, HIGH);
      robotFwdRgt(LOW_SPEED);
#ifdef DEBUG
      Serial.println("robot turns rightward");
#endif
      BTserial.print("Robot turns rightward");
      mode = MANUAL;
      break;     

    case 's':  // robot stops by briefly braking and then romoving motor power
      digitalWrite(LEDpin, LOW);
      robotStop(); 
#ifdef DEBUG
      Serial.println("robot brakes then stop");
#endif
      BTserial.print("Robot brakes then stops");
      mode = MANUAL;
      break;

    default:
      digitalWrite(LEDpin, LOW);
      mode = NO_COMMAND;
#ifdef DEBUG
      Serial.print("NOT RECOGNISED: ");
      Serial.println(data);
#endif
      BTserial.print("Error!");
    }  // end of switch
  } else {  // no character received
    mode = NO_COMMAND;
  }
  return mode;
} // end of command processor


/**************************************************************************
 *  Distance measurement and scanning functions  
***************************************************************************/

// function to measure distance in inches using the ultrasonic rangefinder
float measureDistance(){

  long duration; // variable to hold the distance measurement in microseconds
  
  // Clear the trigger pin
  digitalWrite(TRIG_PIN, LOW);
  delayMicroseconds(2);
  
  // Set the trigger pin HIGH for 10 micro seconds
  digitalWrite(TRIG_PIN, HIGH);
  delayMicroseconds(10);
  digitalWrite(TRIG_PIN, LOW);
  
  // Read the echoPin, return the sound wave travel time in microseconds
  duration = pulseIn(ECHO_PIN, HIGH);
  
  // Calculate the distance
  return duration/74.0/2.0;  // conversion of microseconds to inches
  
}  // end of measureDistance()


// function to scan for open space ahead by pivoting the robot.  Returns true of OK ahead, false if stuck
bool scan(int direction) {
  
  const int LEFT = 0;   // direction constant; left is 0, right is other 
  const int MAX_PIVOTS = 5; // declare stuck if exceed this number of pivots
  int pivotCount = 0;
  
  while (pivotCount++ < MAX_PIVOTS) {
    if (direction == LEFT) {
      robotLeft(SLOW_SPEED);
    } else {
      robotRight(SLOW_SPEED);
    }
    delay(PIVOT_TIME);
    robotStop();

    // is it clear ahead?
    if(measureDistance() >= CLEAR_AHEAD) {
      return true;  // break out of loop and return that OK to move ahead
    }    
  }

  // hit the max number of pivots without finding open space ahead  
  return false;
  
}  // end of scan()

/**************************************************************************
 *  Robot Movement Functions 
***************************************************************************/

// function to move robot forward at commanded speed
void robotForward(int speed){
  forward(MOTORA, speed);
  forward(MOTORB, speed);
  return;
}

// function to turn robot left at commanded speed
void robotLeft(int speed){
  forward(MOTORA, speed);
  backward(MOTORB, speed);
  return;
}

// function to turn robot right at commanded speed
void robotRight(int speed){
  backward(MOTORA, speed);
  forward(MOTORB, speed);
  return;
}

// function to move the robot backward at commanded speed
void robotBack(int speed){
  backward(MOTORA, speed);
  backward(MOTORB, speed);
  return;
}

// function to turn the robot rightward at commanded speed
void robotFwdRgt(int speed){
  forward(MOTORA, speed*0.75);
  forward(MOTORB, speed);
  return;
}

// function to turn the robot leftward at commanded speed
void robotFwdLft(int speed){
  forward(MOTORA, speed);
  forward(MOTORB, speed*0.75);
  return;
}
  
// function to stop the robot
void robotStop(){
  //first apply the brakes
  brake(MOTORA);
  brake(MOTORB);
  delay(500);

  // now release the breaks so the motor leads are floating
  stop(MOTORA);
  stop(MOTORB);
}

/**************************************************************************
 *  Low Level Motor Movement Functions 
***************************************************************************/

// function to spin a motor forward
void forward(int motor, int speed){
  // clamp the speed between 0 and 255
  if(speed < 0){
    speed = 0;
  } else if(speed > 255){
    speed = 255;
  }
  // set up a motor to go forward at the indicated speed
  switch(motor){
    case MOTORA:
      digitalWrite(AIN1, LOW);
      digitalWrite(AIN2, HIGH);
      analogWrite(PWMA, speed);
      break;     
    case MOTORB:
      digitalWrite(BIN1, LOW);
      digitalWrite(BIN2, HIGH);
      analogWrite(PWMB, speed);
      break;    
    default:
      break;
  }
  return;
} // end of forward()

// function to spin a motor backward
void backward(int motor, int speed){
  // clamp the speed between 0 and 255
  if(speed < 0){
    speed = 0;
  } else if(speed > 255){
    speed = 255;
  }
  // set up a motor to go backward at the indicated speed
  switch(motor){
    case MOTORA:
      digitalWrite(AIN1, HIGH);
      digitalWrite(AIN2, LOW);
      analogWrite(PWMA, speed);
      break;     
    case MOTORB:
      digitalWrite(BIN1, HIGH);
      digitalWrite(BIN2, LOW);
      analogWrite(PWMB, speed);
      break;    
    default:
      break;
  }
  return;
} // end of backward()

// function to stop a motor
void stop(int motor){
  switch(motor){
    case MOTORA:
      digitalWrite(AIN1, LOW);
      digitalWrite(AIN2, LOW);
      digitalWrite(PWMA, HIGH);
      break;     
    case MOTORB:
      digitalWrite(BIN1, LOW);
      digitalWrite(BIN2, LOW);
      digitalWrite(PWMB, HIGH);
      break;    
    default:
      break;
  }
  return;
} // end of stop()

// function to brake a motor
void brake(int motor){
  switch(motor){
    case MOTORA:
      digitalWrite(AIN1, HIGH);
      digitalWrite(AIN2, HIGH);
      digitalWrite(PWMA, LOW);
      break;     
    case MOTORB:
      digitalWrite(BIN1, HIGH);
      digitalWrite(BIN2, HIGH);
      digitalWrite(PWMB, LOW);
      break;    
    default:
      break;
  }
  return;
} // end of brake()

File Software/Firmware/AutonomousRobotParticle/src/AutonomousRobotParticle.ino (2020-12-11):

/* Basic Autonomous Robot (Using Particle Photon): The robot can be controlled manually via an app (Basic Robot Movement) and can also be placed
 *	into autonomous mode.  When in autonomous mode, the robot uses the HC-SR04 ultrasonic range finder to detect an
 *	obsticle in front. If forward movement is obstructed, the robot pivots and measures to find an open path ahead and then
 *	continues forward on that path until again obstructed or commanded out of the autonomous mode.  The robot delares that it is
 *	stuck if it cannot find an open path within a predetermined number of pivots/distance measurements.  If the robot is stuck 
 *	in this manner, it automatically exits autonomous mode and must be commanded manually again via the app.
 *  
 *	This version of the robot has three ultrasonic rangefinders.  The main one is pointed dead forward.  There is also a rangefinder
 *	looking to the left (about 45 degrees) and to the right (about 45 degrees).  The left and right rangefinders detect if the robot has
 *	moved too close to one side.  If so, the robot pivots the other way until the side sensor is cleared.  If the sides are clear,
 *	the robot tries to move forward and avoids obstacles ahead, as described above.
 *  
 *	The micorcontroller used for this project is a Particle Photon.  A 74HC595 shift register is used to expand the Photon's I/O's.
 *	Pin assignements are as follows:
 *  
 * 	Shift Register (SR1) controls: SHIFT_CLK = D5; REG_CLK = A0; SHIFT_DATA = D6
 *
 *	Forward ultrasounic rangefinder:  Trigger pin = SR1 QF (decimal value = 32); echo pin = D3
 *	Left ultrasounic rangefinder:  Trigger pin = SR1 QE (decimal value = 16); echo pin = D4
 *	Right ultrasounic rangefinder:  Trigger pin = SR1 QG (decimal value = 64); echo pin = D2
 *  
 *	Left motor (motor A):  in1 = SR1 QC (decimal value = 4); in2 = SR1 QD (decimal value = 8); PWM pin = D0
 *	Right motor (motor B):  in1 = SR1 QB (decimal value = 2); in 2 = SR1 QA (decimal value = 1); PWM pin = D1
 *  
 *	Bluetooth module:  serial1 Photon Rx connected to BT module Tx; Photon Tx connected to BT module Rx
 *  
 *	LED: Photon: D7.  PCB LED: SR1 QH (decimal value = 128)
 *  
 *	This version is compatible with AI2 app version 2.0.  This version adds reporting of the measured front and side distances
 *	back to the app when the robot is in AUTO mode.
 *  
 *	by: Bob Glicksman, Jim Schrempp, Team Practical Projects
 *		version 3.16 12/11/2020
 *			When blocked front robot enters "avoid front" mode. It will pivot in a 
 *			direction until the front is clear, or the FRONTBLOCKED_LIMIT_MS is exceeded
 *		version 3.15 12/4/2020
 *			When blocked front but clear both sides, robot makes a significant pivot
 *		version 3.14 11/9/2020
 *			set distance timeout to 4ms (about 2 feet)
 *			added delay of 1000 microseconds before each measurement - reduce crosstalk
 *		version 3.13 11/4/2020
 *			Cleaned up variable name. Added cmd: to some messages.
 * 		version 3.12 11/3/2020
 * 			Changed front blocked limit to milliseconds. Now set to 20000
 *		version 3.11 11/2/2020
 *			added stop when forward is blocked more than FRONTBLOCKED_LIMIT times
 *   	Version 3.10 10/16/2020
 * 			Pivot right/left now has the 150ms delay again.
 * 			Mainloop 150ms delay added in 3.9 removed.
 * 			TOO_CLOSE_SIDE is now back to 4 inches.
 *		Version 3.9 10/15/2020 
 *			Removed delays from pivots. Robot now moves until a sensor state change.
 *			Removed "scan" since it was just a pivot with no delay.
 *			Now store previous distance and close determination in a global
 *		Version 3.8 10/12/20
 *			Changed NEAR_SIDE to 8.0 and TOO_CLOSE_SIDE to 6.0 to experiment with better side clearance.
 *		Version 3.7 9/29/2020
 *			After our second avoidance experiments. We now remember the most recent Pivot
 *			direction to be our Spin direction if we get in a tight situation.
 *		Version 3.6 9/24/2020
 *			After our avoidance experiments, rewrote the auto loop to be clear and implement
 *			the behaviors we agreed to.
 *		Version 3.5x2 9/17/2020
 *			Moved all action reports to reportAction() to allow removal of duplicate seconds
 *				and standard formatting
 *      Version 3.5x 9/11/2020
 * 			This version will spin in place to avoid a close forward obstacle instead of pivot.
 * 			It will spin for 10 seconds before giving up.
 * 			It handles the case of a narrowing corridor pretty well; it finds its way out.
 * 			There is a behavior in a really tight space where the robot will backup but I'm uncertain
 * 				how to force the robot into that case.
 *		Version 3.4 9/3/2020
 *			If pin A2 is grounded during boot, then the photon will connect to WiFi and the Particle cloud
 *			If connected to cloud, there is a function Autonomous Mode that can be called from the console or Particle app on
 *             smart phone to assert autonomous mode. Doing so also disconnects WiFi to conserve power.
 *		Version 3.3 8/30/2020
 *			Robot will now alter course to avoid a side obstacle that gets NEAR_SIDE distance away. This
 *			causes the robot to glide around obstacles before deciding to stop and pivot.
 *  	Version 3.2 8/25/20
 *      	Added version of pulseIn() with timeout; copied from Particle Community 11/16/16, written by "Ric" 
 *  	Version 3.1 8/23/20
 *      Added semi-automatic system mode declaration so that robot can operate without WiFi
 *	Version 3.0 8/22/20
 *		Converted Arduino robot code to the Photon based PCB, according to pin definitions above.
 *	Version 2.5 01/23/19
 *		Removed 3 ms delay between readings due to additional testing.  Set numPivots to zero when ahead is clear but a side
 *		reading is obstructed.  This way, the Robot can pivot away from the obstruction but if forward path is now blocked, a
 *		random pivot can take place.
 *	Version 2.4 01/21/2019
 *		Added a 3ms delay at the end of each ultrasonic sense. Found empiracally that this eliminated ghost "too close"
 *		measurements in an acoustically challenging environment (my kitchen). No delay would have robot go into avoidance
 *		on occasion in the middle of the floor with plenty of clear space. With a 3ms delay I never observed this.
 *	version 2.3 01/19/2019
 * 		Now do ahead check first and only do side check if ahead is clear.
 *		Now always sense distance after movement, before making any decisions. Avoids some movement loops.
 *	version 2.2 01/18/2019
 *		Added random direction when front is too close
 *		Moved pivot counting into main loop
 *		checkAhead considers both obstruction close and clear ahead distances
 *	version 2.1 01/18/2019
 *		Restructured distancemeasure routine
*/

// Set the system mode to semi-automatic so that the robot will ruyn even if there is no Wi-Fi
SYSTEM_MODE(SEMI_AUTOMATIC);

#define version 3.16
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

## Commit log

2018-11-03 Initial commit of test project data
    Created test and Development folder and subfolders for bluetooth and
    ultrasonic sensor testing. Uploaded hardware, software and descriptive
    text to each sub folder, as required.
2018-11-03 Added ReadMe for the Ultrasonic Sensor test
2018-11-05 Added firmware and app code to send data
    Messages are sent from the Arduino to the app over bluetooth in response
    to commands to change the LED state. The app polls for received
    bluetooth data on a 1 second timer and reds and displays the data
    accordingly.
2018-11-12 Added motor control schematic
2018-11-13 Added datasheets for motor driver module
2018-11-13 Completed test firmware
    implemented and test high and low speed forward and backward motion plus
    stop and brake functionality.
2018-11-13 Added CAD file
    Added a Hardware folder and the laser cutter CAD file for the
    electronics platform.
2018-11-14 Added robot assembly instructions
    Added scan of robot manufacturer's assembly instructions. Added some
    folders for organizational purposes.
2018-11-29 Added sweep distance test
    Added code to test out the ultrasonic rangefinder mounted on a servo at
    the front of the robot. Test to calibrate the sweep delay time to give
    accurate and repeatable distance results.
2018-11-30 Changed BT Rx pin for Yun compatibility
    Changed the robot firmware and BT test firmware to use pin 10 for
    received serial data for Yun/Leonardo compatibility. Also edited the
    returned messages for BT commands to make them more meaningful. Made
    defined constants for BT TX and Rx pins. Likewise, changed the BT
    serial pins on the BT test firmware and also made changes on the
    schematic diagrams to reflect this pin change.
2018-11-30 Updated pin assignments in ReadMe file
2018-12-02 Updated ReadMe with current project status.
2018-12-08 Autonomous firmare
    Updated firmware to version 1.1 featuring autonomous operation of the
    robot. If the robot encounters an obstacle ahead, it randomly chooses a
    direction to pivot. The robot pivots in that direction and measures
    distance ahead until either finds an open pathway to proceed forward or
    else it gives up ("stuck") and defaults back to the manual mode. Readme
    has been updated accordingly.
    [BasicAutonomousRobotSlowPivot.ino]
2018-12-09 Eliminated the servo
    The servo fell off in testing, so I took it out of the hardware and the
    code altogether. I also cleaned up the code and readme.
2018-12-21 Updated firmware and ReadMe
    Added left and right side ultrasonic sensors at 45 degree angles off of
    front and updated firware to process these sensor in order to avoid the
    robot hitting a wall obliquely. Updated readMe accordingly.
2018-12-21 Added photo of 3 sensor robot
2018-12-23 Revert "Added photo of 3 sensor robot"
    This reverts commit 8b5abbcf5b6712b8ba0c0cd571c21a58c1b55ae2.
2018-12-31 pulled button color changes into one procedure
2019-04-12 Photon Controller Hardware Test
    Schematic for Photon Controller breadboard hardware test posted. Photon code posted that integrates bluetooth and motor control; but not yet shift registers or US integration.
2019-04-13 Motor Test
    Added a motor control test that uses the shift register to control motor function/direction, as per the schematic. The motor control test is based upon a similar test routine for the Arduino Uno vers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
2019-04-15 Create Photon_Robot_US-test.ino
    This test routine tests out three HC-SR04 ultrasound modules whose triggers are via the shift register and echo pins go to 5v tolerant inputs on the Photon. A new reading is taken from a sensor and p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
2019-04-22 Update RobotController.pdf
    Added wiring for larger motor controller module and connectors for spare SR and spare Photon pins.
2019-04-24 Update RobotController.pdf
    Reduced schematic to one SR and one level converter in order to reduce board area. Added expansion connectors.
2019-05-02 Completed PCB
    I added the Eagle schematic and board files for the completed (v1) PCB.
    [RobotController.brd, RobotController.sch]
2019-05-05 Create Robot Controller PCB Parts List.xlsx
    Preliminary parts list for the Robot Controller PCB. This parts list only contains parts on the PCB. It does not contain external robot parts: robot body, motors, batteries/holder, ultrasonic modules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
    [Robot Controller PCB Parts List.xlsx]
2020-08-22 Create AutonomousRobotParticle.ino
    This is the Photon version of the earlier Arduino code. It supports the Photon based hardware configuration of the Robot PCB circuit. Funtionality is identical to the previous Arduino version.
2020-08-22 Photon Robot HW and FW
    Photon PCB based robot photos, parts list, Schematic, Eagle Files, and Firmware added to this repository.
    [Robot Controller PCB Parts List.xlsx, RobotController.brd, RobotController.sch]
2020-09-03 3.4 grounding A2 causes WiFi connect
2020-09-03 correction to disable default Autonomous mode
    [AutonomousRobotParticle.ino]
2020-09-05 blink LED on each measurement cycle
2020-09-06 Cleaned up and Added Parts List
    Cleaned up this repository with the PCB version. Updated the PCB Parts List and added a Robot overall parts list. Parts lists are now in PDF format.
    [Robot Controller PCB Parts List.xlsx]
2020-09-11 3.5x spin for avoid
    [AutonomousRobotParticle.ino]
2020-09-17 Removed legacy test code.
    Much of this development and test code was for the Arduino breadboard and not for general publication.
    [Robot Controller PCB Parts List.xlsx, RobotController.brd, RobotController.sch]
2020-09-25 front avoid is now random direction
    [AutonomousRobotParticle.ino]
2020-10-13 Update AutonomousRobotParticle.ino
    Changed defined constants TOO_CLOSE_SIDE to 6.0 and NEAR_SIDE to 8.0 (added 2" to each). Intent is to see if chair leg avoidance is improved.
    [AutonomousRobotParticle.ino]
2020-10-16 3.10 to get it avoiding again
    [AutonomousRobotParticle.ino]
2020-11-04 3.12 front blocked is milliseconds
2020-11-08 new sensor test folder
2020-12-11 3.16 avoid front mode pivots significantly
    [AutonomousRobotParticle.ino]

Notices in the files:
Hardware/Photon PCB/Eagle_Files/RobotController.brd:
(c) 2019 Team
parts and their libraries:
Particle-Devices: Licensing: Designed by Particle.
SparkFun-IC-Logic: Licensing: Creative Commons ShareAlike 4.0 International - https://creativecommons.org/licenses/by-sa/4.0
